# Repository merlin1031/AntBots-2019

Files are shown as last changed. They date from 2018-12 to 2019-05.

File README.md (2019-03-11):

# AntBots
+ Robot Warrior (AntClass)
+ Robo Wars in der Ant-Class aus dem 3D Drucker
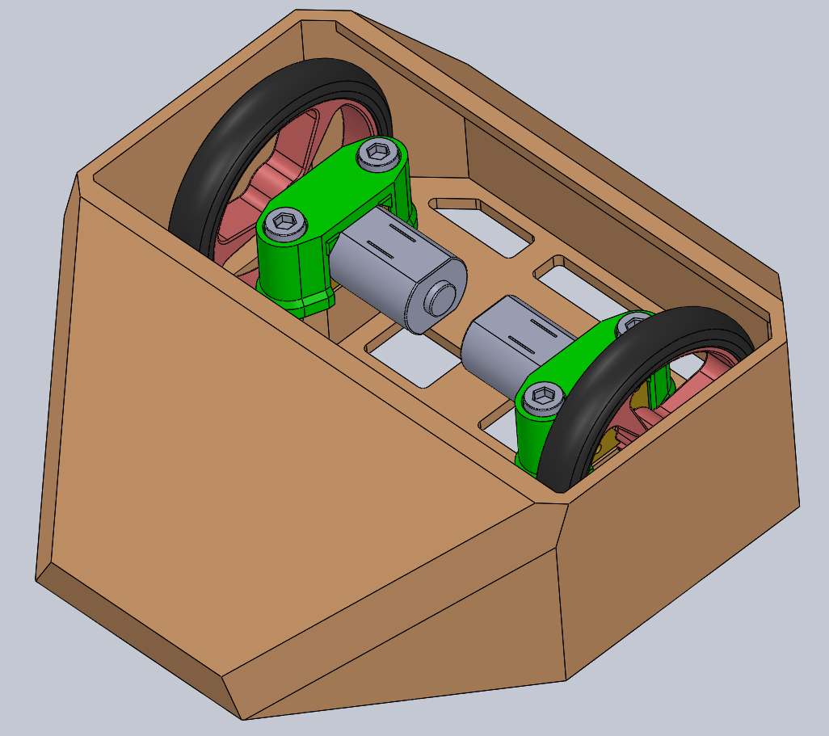
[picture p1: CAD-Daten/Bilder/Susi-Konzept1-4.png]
Susi - AntBot

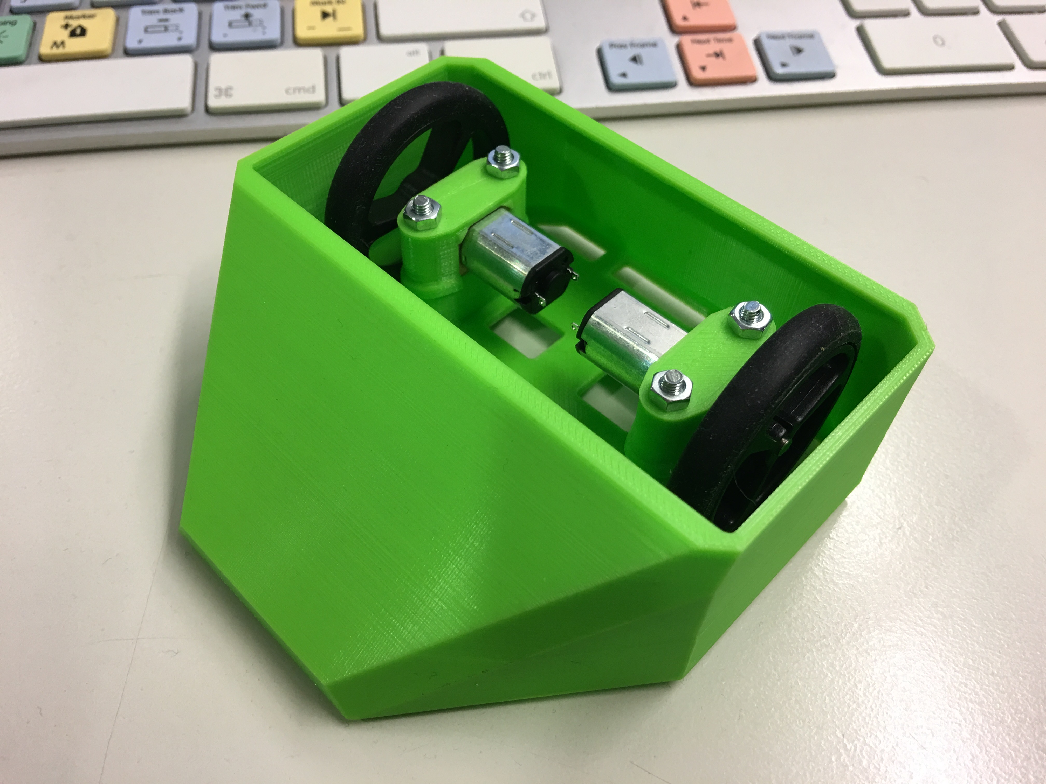
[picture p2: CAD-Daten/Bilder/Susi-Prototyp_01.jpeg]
Susi - AntBot Prototyp


# Spezifikationen
+ Dimensionen max. 10x10x10 cm
+ Gewicht: max. 150g
+ Antrieb: 2S (7,4V)
+ Motor: Geriebemotor 6V, Übersetzung 1:200
+ Räder: Pololu 40x7mm Gummi

# CAD
+ Konstruktion mit SolidWorks 2017/18
+ Slicing und 3D-Druck: Repetier Host und Creality Ender 3

# Gewichtsübersicht
| Komponente | Gewicht [g]|
| --- | ---|
| Empfänger FrySky D4R-II | 4 |
| Empfänger 2.4G 4CH Mini Frsky D8 (banggood) | 2 |
| Akkukabel JST-BEC Buchse ca. 8cm Kabel | 1 |
| Lipo Akku 3S 800mA Turnegy 20-30C | 47 |
| Lipo Akku 3S 500mA Turnegy 20-30C | 33 |
| Lipo Akku 3S 350mA LemonRC 35C | 24 |
| 5V BEC 2A (Eckstein / D24V50F5) | 2 |
| Diatone 5V BEC V2.0 (flyingfolk) | 1 |
| ESC Pololu A4990 (ohne Kabel) | 1 |
| Susi Frame PLA incl. Kugelroller/Motoren/Räder | 86 |
| Schraube M3x30 | 1 |

# Bezugsquellen
## Schrauben
+ Inbus Schrauben DIN 912: [Edelstahlschrauben M3 DIN 912](https://gedex-shop.de/de/schrauben/ZYLINDERSCHRAUBEN/Zylinderkopf-DIN-3699/DIN-912-M3-Innensechskantschrauben-mit-Zylinderkopf-Edelstahl-rostfrei-A2-3700/)

## Antrieb
+ Rad:[Pololu Wheel 40×7mm](https://eckstein-shop.de/Pololu-Wheel-407mm-Pair-Black)
+ Getriebemotor: [V-TEC Micro DC Motor Gleichstrom Getriebemotor 10x8mm 6V](https://eckstein-shop.de/V-TEC-Micro-DC-Motor-Gleichstrom-Getriebemotor-10x8mm-10x12mm-12x13mm-3V-6V-17-560RPM)
+ Getriebemotor Alternative: [Orlandoo OH35P01 KIT RC Car Parts Gear Motor - 300](https://www.banggood.com/custlink/v3KGERK978)
Leider bietet Eckstein nur Getriebe bis zur Übersetzung 1:200 an (Stand Dez. 2018). Nach den ersten Fahrversuchen wird sich zeigen ob diese Übersetzung "zu langsam" ist. Falls ja müsste eine kleinere Übersetzung wie z.B. diese 1:300 eingestezt werden.
+ ESC: [ Dual Motor Driver Carrier dual H-bridge](https://eckstein-shop.de/Pololu-A4990-Dual-Motor-Driver-Carrier-dual-H-bridge)
+ ESC Alternative: [DasMikro 2S6A Micro Dual Bi-Directional Speed Controller for Tank Crawler and Boat without Brake](https://www.banggood.com/custlink/vmGmdEGiuN)
Interessant ist die Version A mi eingebauem Mischer. Dabei ist Signal 1 für die Motorendrehzahl (vorwärts / rückwärts) zuständig und Signal 2 für die Richtung (links / rechts).
Mit dem Mischer wird es dann möglich den Roboter mit einer handelsüblichen, günstigen Colt-Anlage zu steuern. In der Regel besitzen diese Sender keine Mischer um das softwareseitig einstellen zu können. Bei normalen Knüppel-Sendern (z.B. FrySky 9D Plus) kann dies über einen etsprechnden Software-Mischer im Sender eingestellt werden.
+ 5V BEC: [Mini BEC 5V 2A V2 bis 6S Lipo!](http://flyingfolk.com/Voltage-Regulators-Spannungsregler/FPV-Mini-UBEC-BEC-5V-2A-2S-6S-LiPo-Step-Down-Spannungswandler)

jetzt hier eine Änderung zum Test

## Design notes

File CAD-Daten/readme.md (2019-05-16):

In diesem Ordner werden alle CAD-Modelle abgelegt.

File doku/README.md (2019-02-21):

## was gehört zur Doku?
hier sollten alle Dokumente, ANleitungen, Technische Beschreibungen usw. abgelegt werden, die für das Projekt wichtig sind.
Wichtige Infos und Gedanken können einfach in der README.md Datei (die kann in jedem Verzeichnis existieren) mit einer MarkDown-Script Sprache schnell und einfach zusammengefasst und ohne komplizierte Software notiert werden.
Mit MarkDown-Texten können zu einem späteren Zeitpunkt auch recht schnell die Infos in ein anderes Medium überführt werden. Z.B. als Copy & Paste - Vorlage in einem CMS wie Joomla.

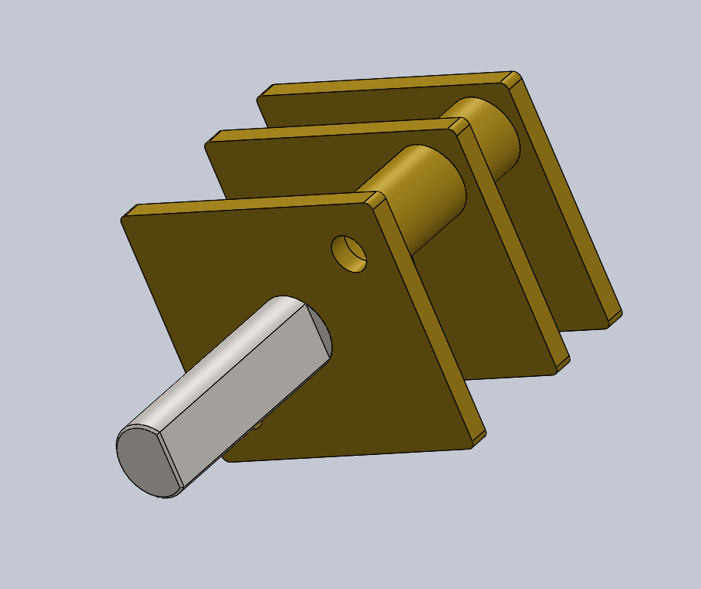
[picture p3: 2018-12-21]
CAD-Daten/Bilder/V-Tec_GetriebeMockup.png

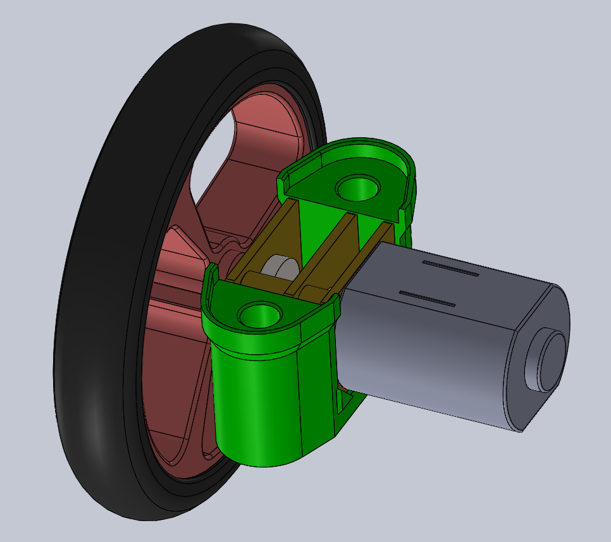
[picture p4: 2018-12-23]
CAD-Daten/Bilder/Susi-Antriebseinheit_2.png

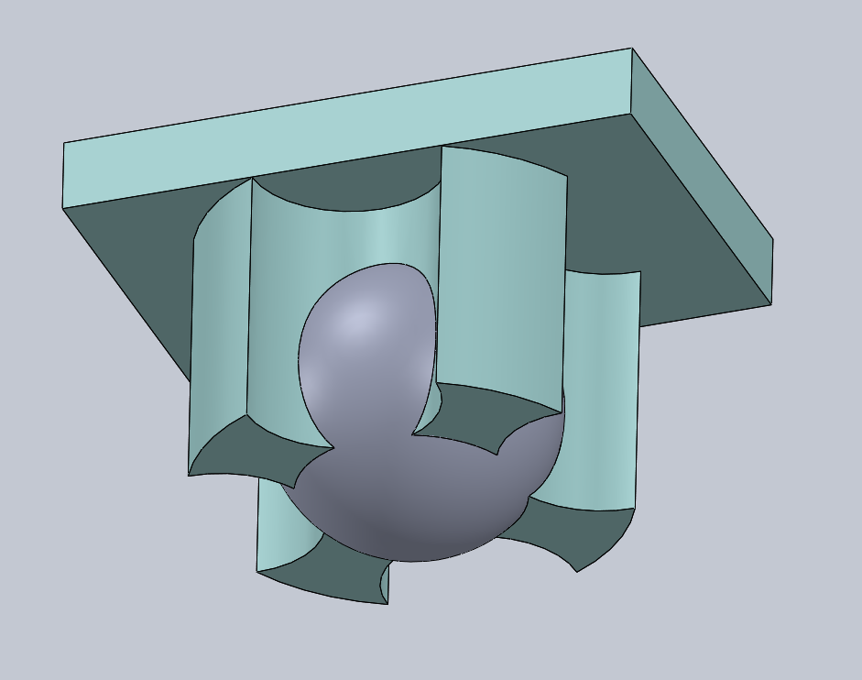
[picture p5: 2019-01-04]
CAD-Daten/Bilder/KugelRoller_Konzept1.png

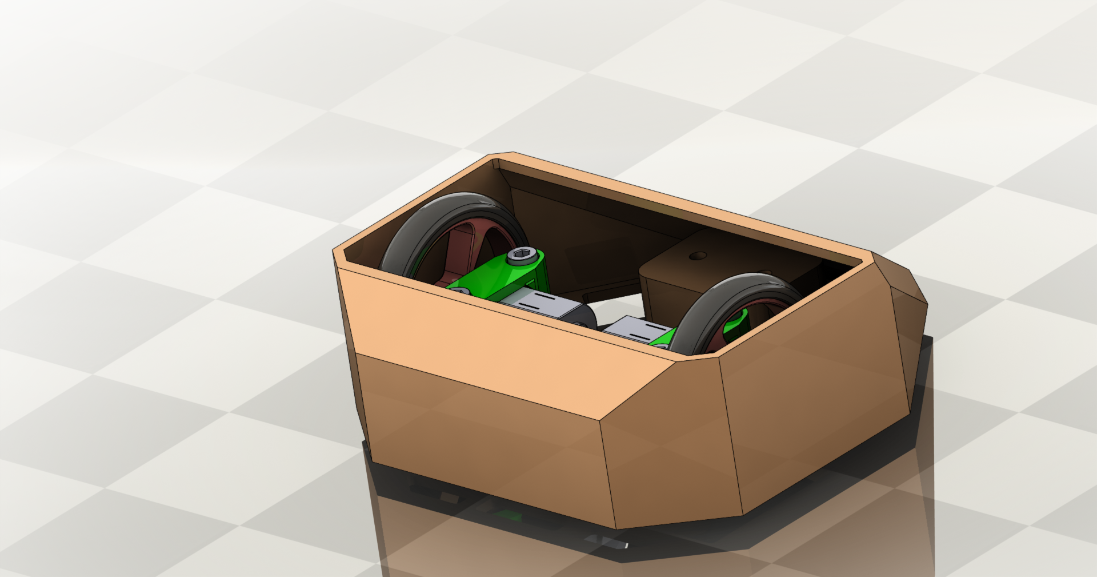
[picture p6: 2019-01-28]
CAD-Daten/Bilder/Susi_Rendering_02.png

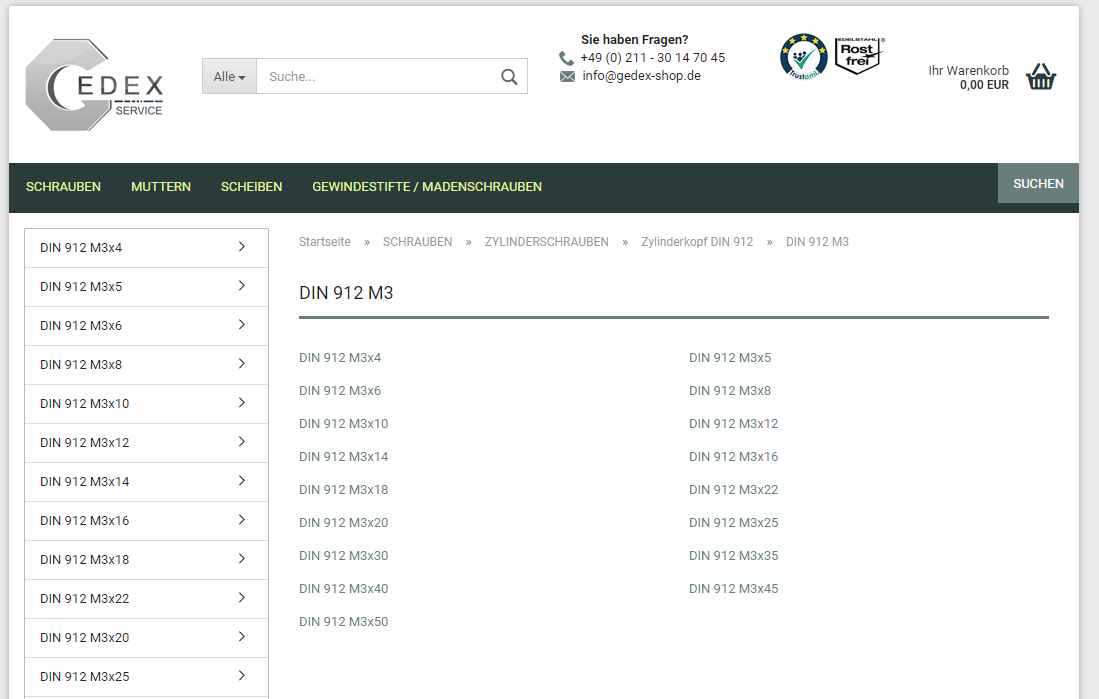
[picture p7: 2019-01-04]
CAD-Daten/Bilder/Din912_M3x10_GeDex_Onlineshop.png

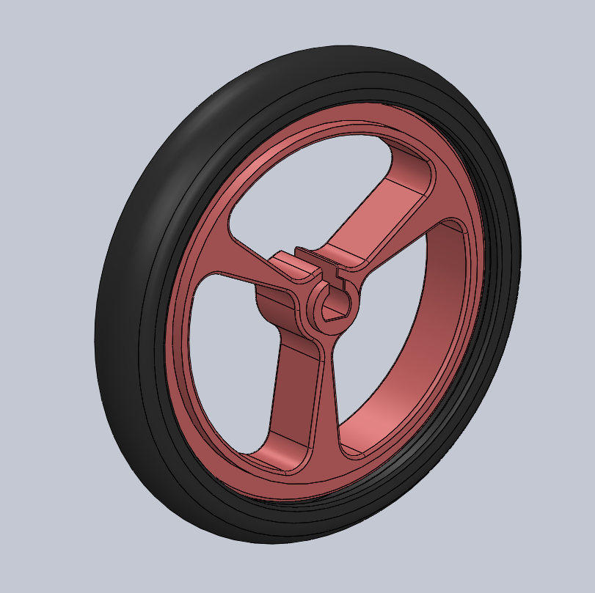
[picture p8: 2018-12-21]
CAD-Daten/Bilder/PololuWheel_Rad.png

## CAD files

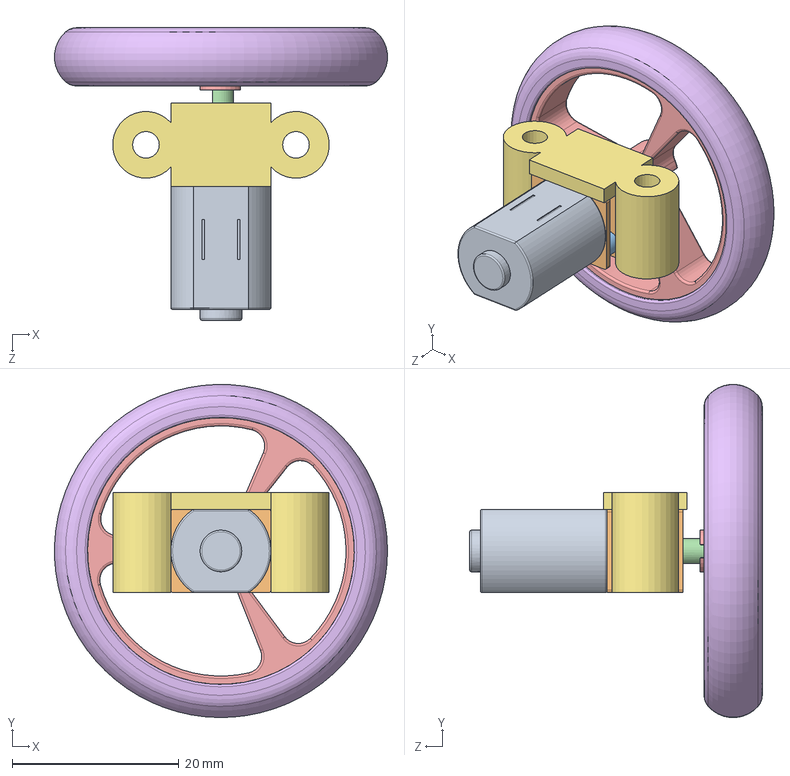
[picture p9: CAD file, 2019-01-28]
CAD-Daten/Susi_AntriebsEinheit.SLDASM
40.0 x 40.0 x 35.1 mm
V-Tec_MicroMotor_6V
V-Tec_GetriebePlatteMockup x 3
V-Tec_DistanzRohr x 4
V-Tec_AntriebsWelle
Pololu_Wheel_40x7_Felge
PololuWheel_40x7_Reifen
V-Tec_GetriebeHalter

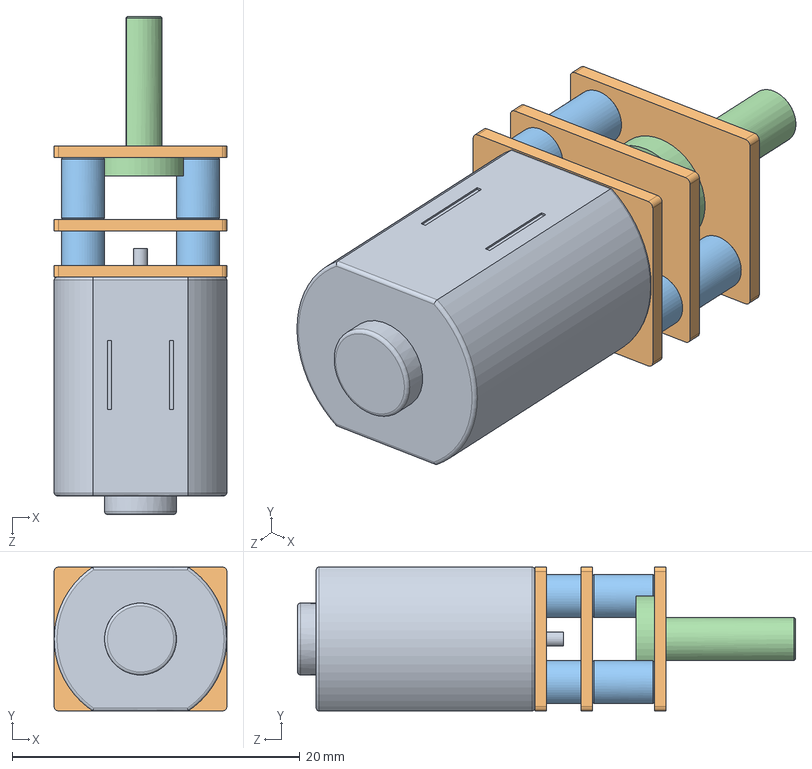
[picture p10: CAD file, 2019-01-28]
CAD-Daten/V-Tec_MotorEinheit.SLDASM
12.0 x 10.0 x 34.6 mm
V-Tec_MicroMotor_6V
V-Tec_GetriebePlatteMockup x 3
V-Tec_DistanzRohr x 4
V-Tec_AntriebsWelle

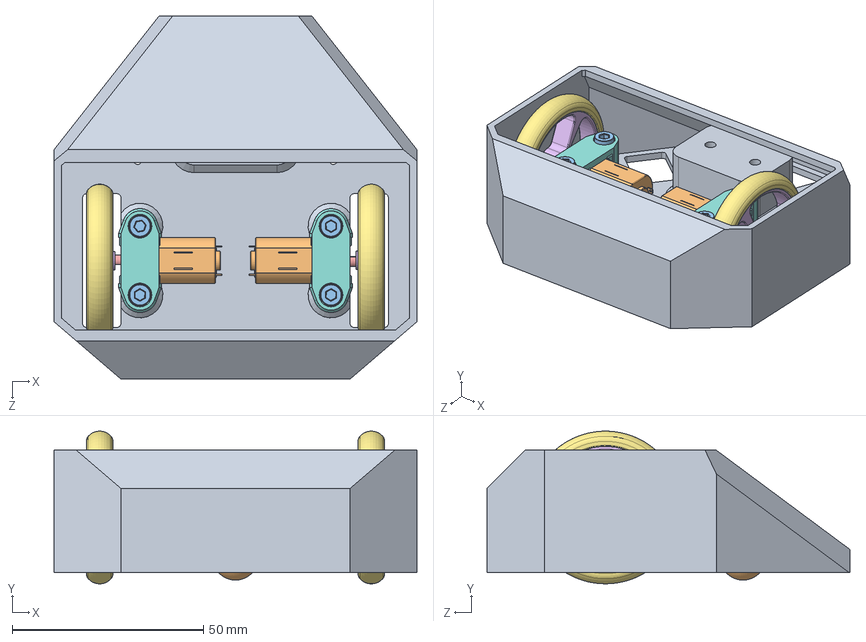
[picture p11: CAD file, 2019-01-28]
CAD-Daten/Susi_AntWarrior.SLDASM
95.0 x 40.0 x 95.0 mm
Susi_FrameBottom
V-Tec_MicroMotor_6V x 2
V-Tec_GetriebePlatteMockup x 6
V-Tec_DistanzRohr x 8
V-Tec_AntriebsWelle x 2
Pololu_Wheel_40x7_Felge x 2
PololuWheel_40x7_Reifen x 2
V-Tec_GetriebeHalter x 2
KugelAufnahme
Kugel 12mm
Zylinderkopf_Din912 x 4

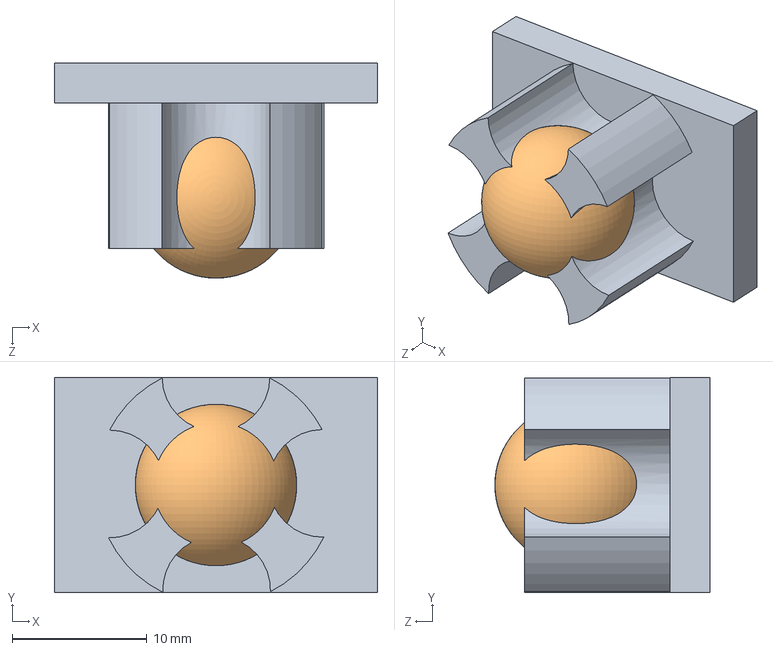
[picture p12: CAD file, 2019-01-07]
CAD-Daten/KugelRoller.SLDASM
24.0 x 16.0 x 16.0 mm
KugelAufnahme
Kugel 12mm

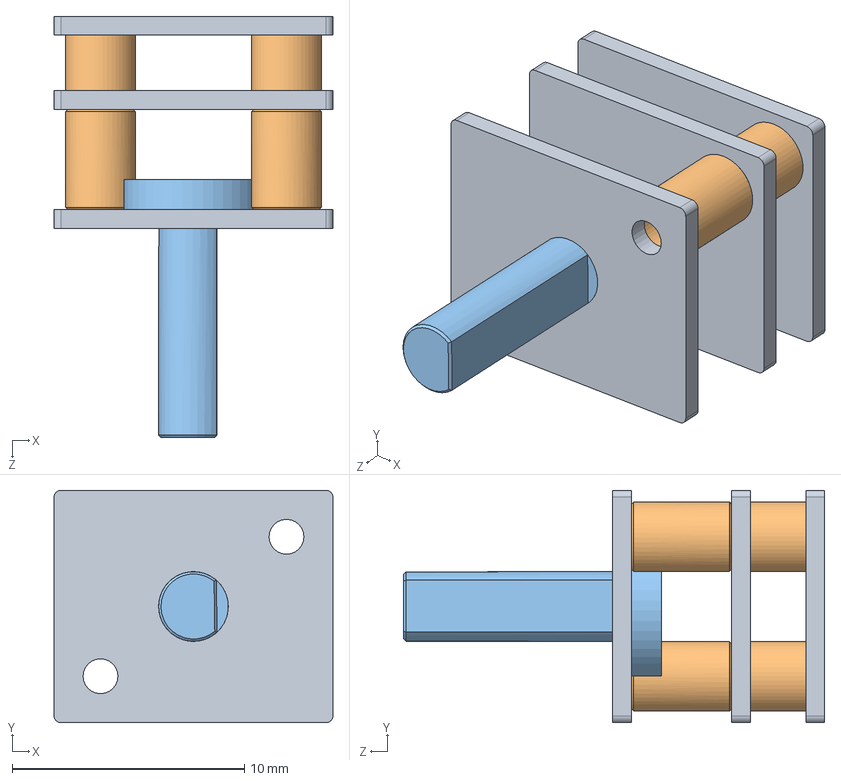
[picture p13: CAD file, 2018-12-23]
CAD-Daten/V-Tec_GetriebeMockup.SLDASM
12.0 x 10.0 x 18.1 mm
V-Tec_GetriebePlatteMockup x 3
V-Tec_DistanzRohr x 4
V-Tec_AntriebsWelle

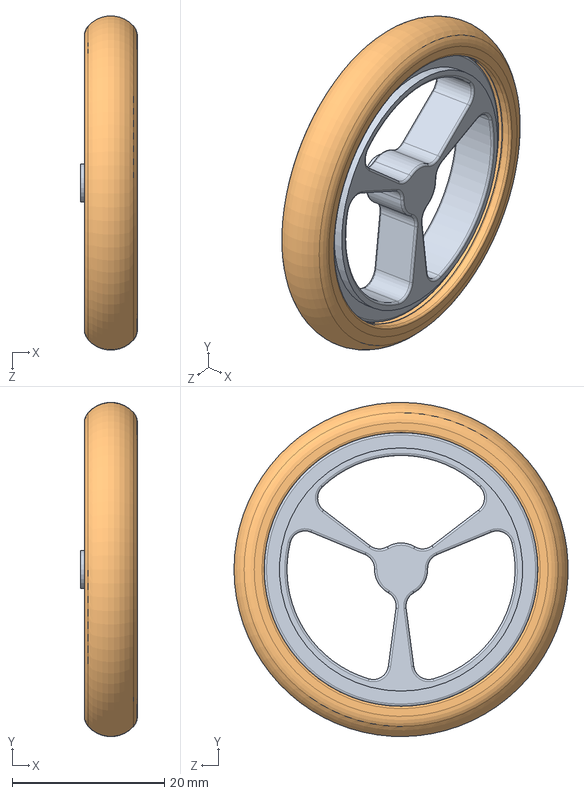
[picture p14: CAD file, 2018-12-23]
CAD-Daten/PololuWheel_Rad.SLDASM
7.50 x 44.0 x 43.9 mm
Pololu_Wheel_40x7_Felge
PololuWheel_40x7_Reifen

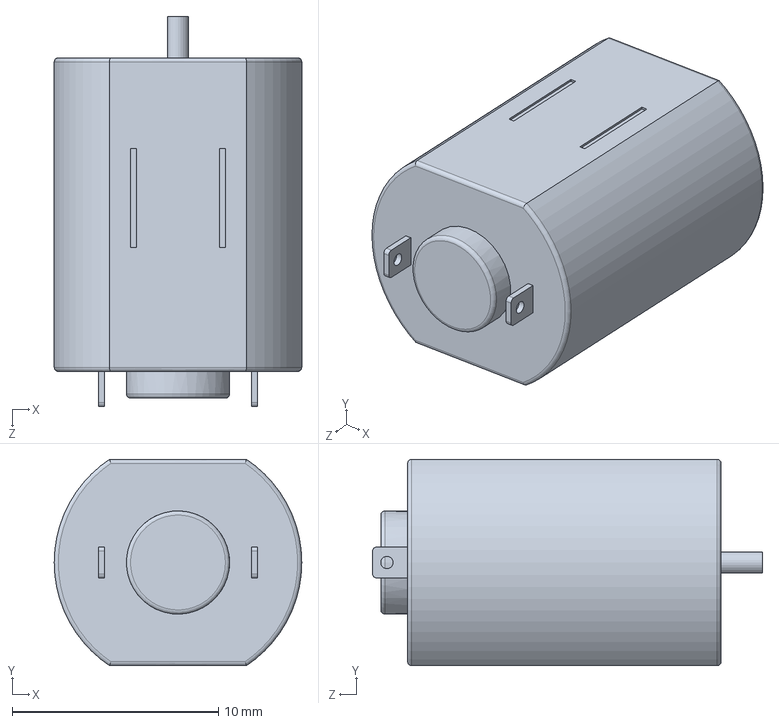
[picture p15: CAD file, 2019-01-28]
CAD-Daten/V-Tec_MicroMotor_6V.SLDPRT
12.0 x 10.0 x 18.9 mm

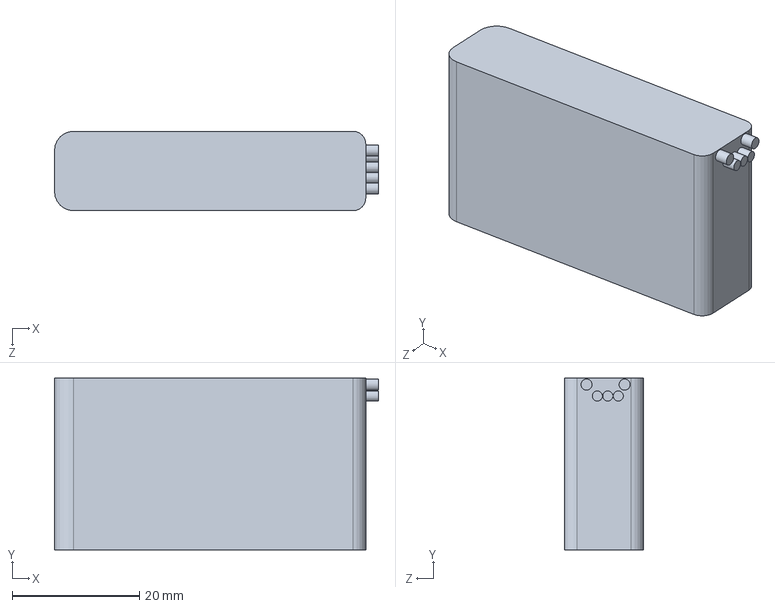
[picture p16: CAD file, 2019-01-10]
CAD-Daten/Lipo_2S_350mA_LemonRC.SLDPRT
51.0 x 27.0 x 12.5 mm

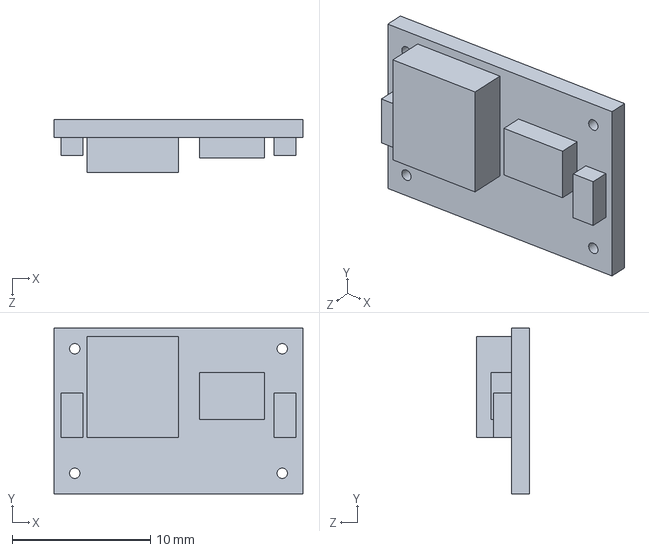
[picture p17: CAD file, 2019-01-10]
CAD-Daten/BEC 5V 2A Diatone V2 DT-EL0011.SLDPRT
18.0 x 12.0 x 3.85 mm

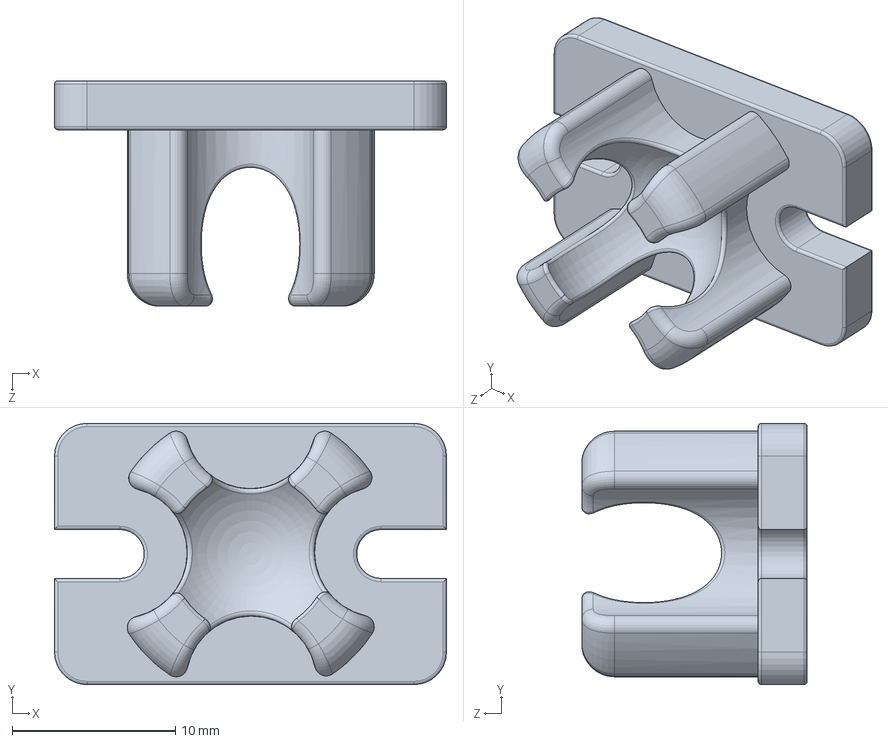
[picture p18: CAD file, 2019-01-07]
CAD-Daten/KugelAufnahme.SLDPRT
24.0 x 16.0 x 13.8 mm

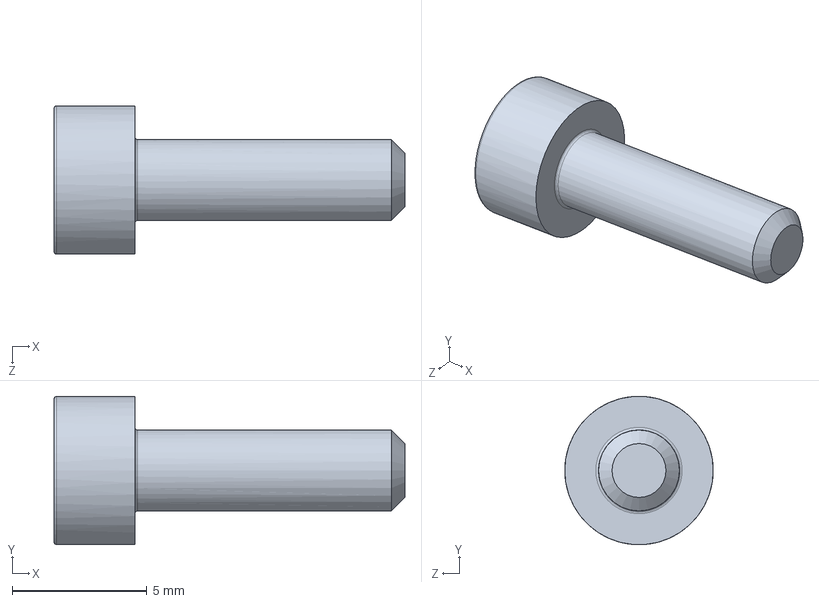
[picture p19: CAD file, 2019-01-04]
CAD-Daten/Zylinderkopf_Din912.SLDPRT
13.0 x 5.49 x 5.50 mm

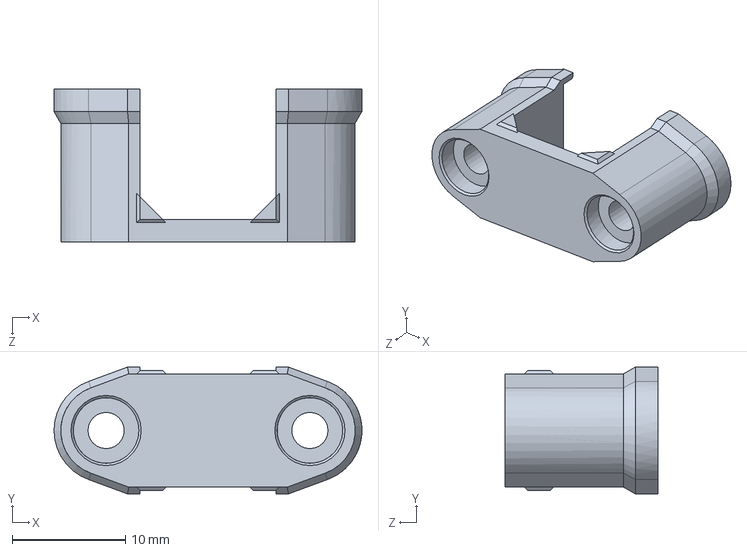
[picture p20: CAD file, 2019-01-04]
CAD-Daten/V-Tec_GetriebeHalter.SLDPRT
27.2 x 11.2 x 13.5 mm

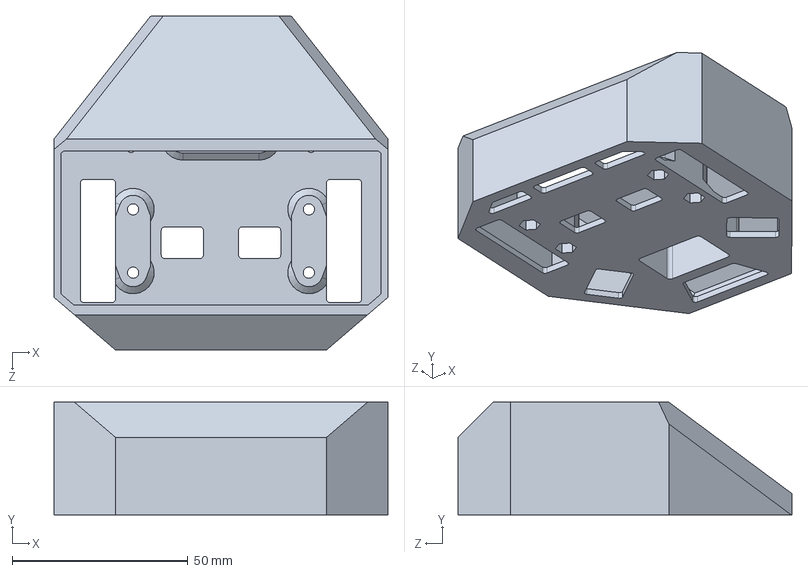
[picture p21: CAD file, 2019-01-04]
CAD-Daten/Susi_FrameBottom.SLDPRT
95.0 x 32.0 x 95.0 mm

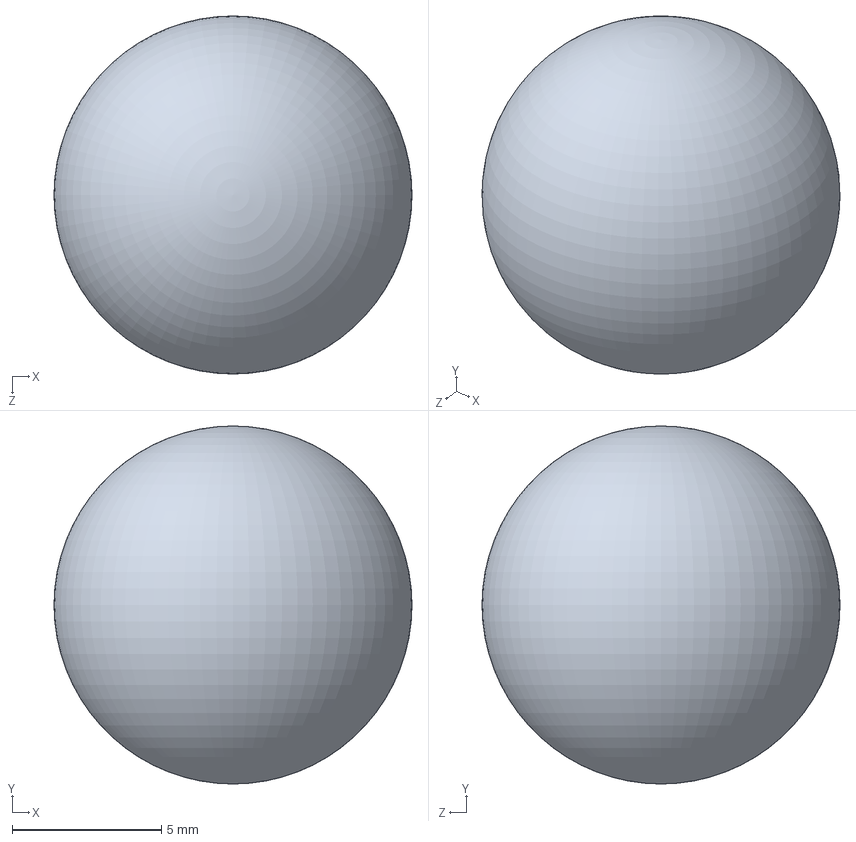
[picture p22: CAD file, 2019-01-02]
CAD-Daten/Kugel 12mm.SLDPRT
12.0 x 12.0 x 12.0 mm

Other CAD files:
CAD-Daten/V-Tec_GetriebePlatteMockup.SLDPRT
CAD-Daten/V-Tec_DistanzRohr.SLDPRT
CAD-Daten/PololuWheel_40x7_Reifen.SLDPRT
CAD-Daten/V-Tec_AntriebsWelle.SLDPRT
CAD-Daten/Lipo_2S_350mA_LemonRC.SLDDRW
CAD-Daten/PololuWheel_Rad.SLDDRW
CAD-Daten/Pololu_Wheel_40x7_Felge.SLDPRT
CAD-Daten/Susi_FrameBottom.STL
CAD-Daten/V-Tec_GetriebeHalter.STL

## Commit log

2018-12-21 SW Dateien hinzugefügt
    Test ob Git-Hub mit SolidWorks zurechtkommt
    [PololuWheel_40x7_Reifen.SLDPRT, PololuWheel_Rad.SLDASM, Pololu_Wheel_40x7_Felge.SLDPRT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]
2018-12-21 V-Tec GetriebeEinheit
    V-Tec Getriebe Mockup erstellt
    [V-Tec_AntriebsWelle.SLDPRT, V-Tec_DistanzRohr.SLDPRT, V-Tec_GetriebeMockup.SLDASM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]
2018-12-21 div. Komponenten Bilder
    verschiedene Bilder für die Doku erstellt
2018-12-22 Susi 1. Konzept
    Befestigung Getriebe mit Frame, Reifen Durchmesser angepasst
    [PololuWheel_40x7_Reifen.SLDPRT, PololuWheel_Rad.SLDASM, Susi_AntWarrior.SLDASM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]
2018-12-22 Bilder hinzugefügt
    Bilder Konzept Getriebehalter und Susi-Frame
2018-12-23 Änderungen Getriebehalter
    Änderungen Getriebehalter und Anpassungen am Frame, erster 3D Druck durchgeführt auf Ender3
    [PololuWheel_40x7_Reifen.SLDPRT, PololuWheel_Rad.SLDASM, Pololu_Wheel_40x7_Felge.SLDPRT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]
2019-01-02 Kugelroller eingefügt
    Position der Haupträder nach hinten verschoben, Kugelroller eingefügt
    [Kugel 12mm.SLDPRT, KugelAufnahme.SLDPRT, KugelRoller.SLDASM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]
2019-01-04 Anpassungen nach 1. Druck
    M3 Din912 für Motorbefestigung eingefügt, Nut für M3 Mutter in Frame eingebaut, 1. Probe-Druck Frame durchgeführt, Stabilität ok
    [KugelAufnahme.SLDPRT, KugelRoller.SLDASM, Susi_FrameBottom.SLDPRT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]
2019-01-04 aufräumen
    [Susi_AntWarrior.SLDASM, Susi_AntriebsEinheit.SLDASM, Zylinderkopf_Din912.SLDPRT]
2019-01-05 Alternative ESC und Motoren vn Banggood
2019-01-07 Kugelhalter Details hinzugefügt
    [KugelAufnahme.SLDPRT, KugelRoller.SLDASM, Susi_AntWarrior.SLDASM]
2019-01-08 BilderGröße und Bilder Prototyp
2019-01-09 Akku MockUp
    [Lipo_2S_350mA_LemonRC.SLDPRT, Susi_AntWarrior.SLDASM]
2019-01-10 BEC5V 2A Mockup
    [BEC 5V 2A Diatone V2 DT-EL0011.SLDPRT, Lipo_2S_350mA_LemonRC.SLDPRT, Susi_AntWarrior.SLDASM]
2019-01-26 Renderbilder
    neues SolidWorks installiert, jetzt wieder mit Rendering
    [Susi_AntWarrior.SLDASM]
2019-01-27 Anschlussfanen Motoren
    Anschlussfahnen MOtoren hinzugefügt, Anleitung zum ENtstören von Bürstenmotoren aus dem Web gesucht
    [Susi_AntWarrior.SLDASM, Susi_AntriebsEinheit.SLDASM, V-Tec_MicroMotor_6V.SLDPRT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]
2019-01-28 PDF Dieselpunk FPV Tractor
    interessanter Ansatz für Framebau und Elektronik
2019-01-30 Create ~$BEC 5V 2A Diatone V2 DT-EL0011.SLDPRT
2019-03-17 Add files via upload
    This Dual ESC module is designed for RC micro model tank, crawler and boat DIY.
2019-03-30 Zeichungen erstellt
    [Lipo_2S_350mA_LemonRC.SLDDRW, PololuWheel_Rad.SLDDRW]
2019-05-16 Create readme.md
    erster Eintrag bei CAD-Daten
